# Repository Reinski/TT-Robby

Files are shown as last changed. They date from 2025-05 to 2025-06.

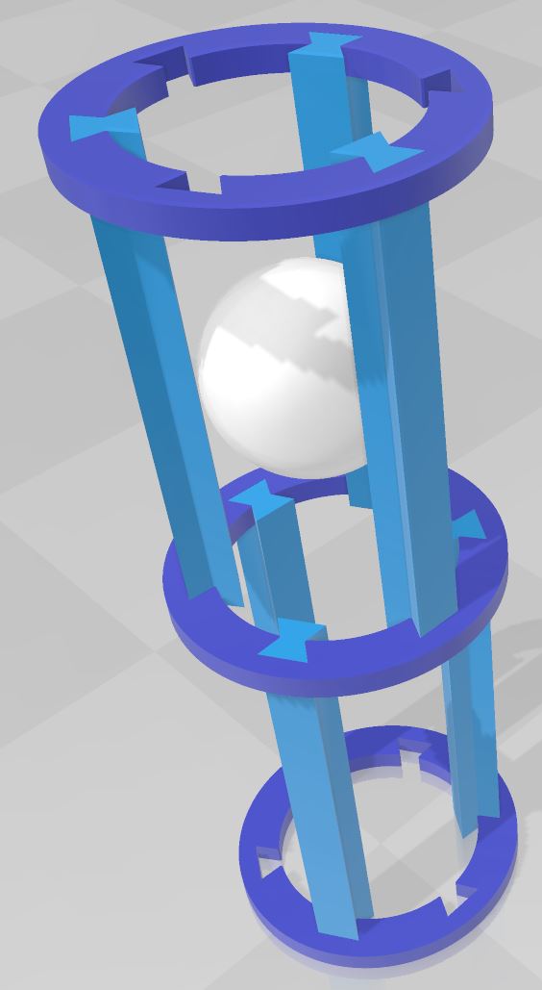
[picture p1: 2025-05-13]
resources/ball_lead_concept.jpg

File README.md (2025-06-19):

# TT-Robby
## Overview
TT-Robby is a hobby project to design a tabletennis ball machine with focus on affordability by hobby players.
The concept is based on using 3D printed parts whereever possible and otherwise cheap components. The tradeoff is a higher requirement of time in comparison to buyable out-of-the-box solutions, invested into printing, assembling and adjusting the whole machine.  
Another goal is high flexibility through modularity in both, construction and programming.
## Getting started
Unfortunately, there is no fool-proof concept that will work out of the box. So this project is still in a tinkering state (PoC). If you want to get a feeling for the basic concept without investing too much time and effort, then I'd suggest the following:
- Print 6x ball_lead-pole_100mm and 3 ball_lead-orthogonal_ring, assemble a straight tube, take a tt-ball and play around with it.
- If you like what you see, print 2 more rings and 3 more poles and add an orthogonal branch in your previous construction (hint: replace one pole with a ring).
- If you still want to continue, then you need to invest some money, as you should start with the electronics now. I find it most satisfying to see the machine fire some balls, so I'd suggest starting with building the Ball Driver:  
  From the BoM below, buy at least 2 DC motors, a raspi pico and the Motor Driver Module plus you'll want some dev equipment like a breadboard, wires, usb-cable etc. plus you'll need some IDE to operate the motors.
- Now, if you're still motivated to go for it, you can have a look at the rest and help finding solutions for all the open issues.
## Bill of material
### Simplest Setup
No side-spin, fix ball direction
- Raspberry Pi Pico W or WH (~8€)
- 2 x DC Toy Hobby Motor - 130 Size 4.5V to 9V (~2€ each)
- 1 x WaveShare DC Motor Driver Module (https://www.waveshare.com/wiki/Pico-Motor-Driver) (~30€)
- 1 x 28BYJ-48 stepper motor 5V DC + ULN2003 driver board (~2.20€ each)
- 2 Rubber rings (50x4mm; Diameter approx. 30mm) 
- Wires + boards
- 3D printing filament
- some tools for printing post-processing and for (dis)assembling (e.g. pliers)
### Max setup
All currently supported features: Top spin, back spin, side-spin, fix ball direction
- Raspberry Pi Pico W or WH (~8€) (Pico2 not tested yet)
- 3 x DC Toy Hobby Motor - 130 Size 4.5V to 9V (~2€ each)
- 1 x WaveShare DC Motor Driver Module (https://www.waveshare.com/wiki/Pico-Motor-Driver) (~30€)
- 2 x 28BYJ-48 stepper motor 5V DC + ULN2003 driver board (~2.20€ each)
- 2 x Sg92r servo motors
- 3 Rubber bands (50x4mm; Diameter approx. 30mm)
- Wires + boards
- 3D printing filament
- some tools for printing post-processing and for (dis)assembling (e.g. pliers)
## Open points
To give a rough overview about the maturity of this project, here are some open issues. Details can be found at the specific components' sections below.
- Ball Feeder with current pushing geometry and stepper motor is not fast enough to serve 1 ball/sec. New conncept is in test, though.
- Concept for Ball Pool must be finalized
- Concept for Ball Recirculation is open
- Concept for Direction Control (automated rotation and tilt) has to be completed. Esp. tilt is missing.
- Power Supply specification for the Ball Driver motors must still be defined.
- Suitability of the 130 size DC toy motors is questionable (although latest tests indicate that two of them are ok for basic funcitonality)
- Wiring and casing geometry is still to be designed
- Control concept and its implementation is incomplete (Controller API)
## Components
This section describes the ball machine's components in detail. The components are listed in alphabetic order.
### Ball Driver
Probably being the most important part of the machine, the Ball Driver is responsible to accelerate the ball with the required attributes of 
- transversal speed
- transversal direction
- spin speed
- spin axis  
  The concept is to have three wheels accelerating the ball from different angles with individual values, so that the forward speed and the rotation speed and axis is determined by the different wheel speeds.
  The forward direction is controlled by the ball lead (always co-axial), so that it can only be controlled by pivoting (left/right) and tilting (up/down) the whole Ball Driver to point into the required direction.
  If a mechanic is implemented to change orientation its minimum requirements shall be:
- pivot angle >= 45°
- tilt angle at least from -45° to +15° (-45° is intended for simulating specific serves, but is certainly not the highest priority)
  In case of downwards tilt a premature release of the ball should be prevented (i.e. gravity should not drag the balls into the driver)
#### Open points
- Power Supply
  Power output from Raspi Pico is too weak for operating the three motors. So a concept is required to provide power to the motors with adequate electrical properties.
  The aim should be:
  - have only one power plug into standard socket (AC)
  - have enough power to operate all motors at full speed
  - have stable power supply for the controller board
  - have the power related elements stored away in some containment to avoid user contact and reduce negative environmental influence (dust, moisture)
  - keep the whole electrical system at an adequate temperature
- Motor Suitability
  The currently used 130 sized DC toy motors are very cheap and have a nice speed, but are very weak and not very responsive to control commands (high inertia-to-power ratio).
  Although they proved capable of driving a ball plain forward at sufficient speed (no spin) - even with just two motors, they must still be testet if they are really suitable under field conditions.
- Orientation Control
  A horizontal swivel has now been designed and seems ok. However, it turns the whole main part of the machine and the decoupling from both, the stand and the Ball Pool, is currently not very satisfying. 
  For the vertical control there is currently no concept implemented.
  A concept should include motor specification, component geometry, ball leading concept for the varying angles.
  Until such a concept is designed, TT-Robby has a fixed ball direction and must be manually oriented into the wanted direction.
- Wiring and Casing
  Wires must be lead in a way that they cannot interfere with the component's operation (turning wheels, moving parts), but still can be easibly mounted and unmounted. This also includes a concept for connectors making the installation more comfortable to the user.  
  Electronic components like the microcontroller on the motor driver shield and also the motors themselves should be located in safe places to provide safety for them and for the operators. An according design is required.
### Ball Feeder
The Ball Feeder has the task to feed the next ball in a controlled manner into the Ball Driver, i.e. directly into the place where the ball is caught by the Ball Driver's wheels. This should happen independently of the Ball Driver's (including the feeder) current orientation, esp. regardless of the relative direction of gravity.
While the Ball Pusher (a turnstile-like design, see below) is able to push a single ball further while holding back the next one, its current geometry prevents it from being able to push the ball far enough into the feeding position.
As an alternative, a piston concept has been designed, which is able to push the ball far enough into the ball driver. However, the current concept takes too long for one sequence, so it needs refactoring.
### Ball Leads
On the whole way from the Ball Pool to the Ball Driver, each ball must always be in a controlled location to avoid disturbances in the operation.
While many machines use tubes or otherwise fully encased constructions to guide the balls in a controlled manner, TT-Robby uses a modular system of combining various segments, basically consiting of 3 co-axial leading poles carried by rings.
The poles are connected to the rings by sticking them through accordingly shaped openings in the rings. Using this principle, more elements can be attached in the same manner either to the rings or to the poles.
### Ball Pool
The Ball Pool is the main reservoir to hold the ball supply for the machine. In normal operation mode it is the only way to feed balls from outside into the machine.  
Designed basically as a big funnel, open at the top and with a ball-sized opening at the bottom, it follows a very simplistic approach.
In the concept phase, a funnel made out of cardboard had been used, which basically fulfilled its task. Meanwhile, a 3d printed ball pool was designed, as integrating the pool in a controlled manner into the machines geometry was problematic with the cardboard-approach.  
However it must be said, that the handling of the 3d-printed ball pool is quite uncomfortable, as it follows the modular concept and as a consequence is not very stable.
#### Open points
- Improve design of the pool itself: It has weak stability when applying force e.g. during assembly.
- Improve ball outlet geometry: Find a statically determined geometry, where all parts go into their pre-defined places.
- Find a concept for reliably supplying balls into the moving part of the machine (i.e. the Ball Driver).
### Ball Pusher
To transport the balls through the whole system (see Ball Leads), finally arriving sequentially at the Ball Driver, they need to be moved independently of their natural tendencies caused by gravity, bouncing etc.  
The Ball Pusher is a cross-shaped wheel (turnstile-like) driven by a step motor, which pushes one ball at a time and lets the next ball move into place. Multiple Ball Pusher components can be attached to Ball Leads whereever required.  
Currently the concept is not used, as instead a more simplistic approach is applied, where the balls are dropping out of the Ball Pool into the Ball Leads and move through them, pulled by gravity.
### Ball Recirculation
After balls have been hit by the player, it would be most convenient to automatically bring them back into the machine, hence creating a full cycle. Most ball machines make use of nets catching the played balls directly near the edges of the table and leading them - dragged by gravity - back into the Ball Pool.  
Despite this being a quite effective concept, it has the downside, that the nets plus their holders are a cost factor and mean quite high effort to assemble before each training session.
Since I am a lazy person, I'm still thinking of an alternative approach.
Until that is found, TT-Robby omits the Ball Recirculation Concept and instead relies on the manual work to collect the served balls and fill them back into the Ball Pool.
### Direction Control / Rotator
The balls' forward direction should be machine-controllable, i.e. the pivot and the tilt of the ball driver must be changeable.  
In the basic setup, this is a manual process by the user simply changing the machine's orientation (see also Machine Mount).
First approach for changing the horizontal direction has been implemented and the name "Rotator" has been established. Since also the tilt is probably controlled by rotation, this name can be used generally.
#### Open Points
- Define overall concept: Orientate the whole machine incl. Ball Pool or orientate just the Ball Driver+Feeder?
- Design mechanical geometry for the selected concept.
- In case of only parts of the whole system change their orientation: Solve problems for a smooth ball transition between static and movable ball leads.
- Define motors to use
- Implement controller logic
### Machine Controller
The Machine Controller is the software running on the Pi Pico and has the task to control the machine parts (motor speeds and orientations). For this it translates the user's requirements (mainly direction, speed, spin and interval) into the technical commands to the motors. It may also be responsible for providing access to the current settings or reflecting them back to the user.
Currently, the plan is to have a REST-API for the user commands which could then be accessed from Apps on a mobile device or even a JavaScript UI running in the local browser.
In its current state the controller program already supports the translation of most user commands into machine control commands and even allows to define ball sequences (changing spin, speed, interval between single balls).
#### Open Points
- REST API
- Security concept (API tokens?)
- Stability tests
- Demonstration UI
### Machine Mount
Where shall TT-Robby be mounted? Currently it must be placed directly on the table surface, but even then it needs some sort of a stand to be designed.  
Idea is to design a simple table surface stand in the first step being easily replacable by other solutions which may be created later.
To achieve this flexibility, a connector concept between the ball machine and the stand shall be implemented.
Options for the stand are:
- Place directly on table
- Attach to table by clamp or something similar
- Place on an own stand (maybe attach to standard camera tripod)
- Direction Control could be implemented in the stand and not into the ball machine itself
#### Open Points
- Design mount connectors
- Design simple stand
- Design flexible mount, allowing rotation and tilt - if this is not a feature of the ball driver alone.
## Specifications
These are the minimum specifications that should be met by the fully configured machine.
- As cheap as possible
- Shot frequency: 1 balls/sec
- Ball forward speed: 100 km/h
- Ball rotation: up to 100 rpm
- Shot direction angle, horizontal rotation: 90°
- Shot direction angle, up/down: 45°
- Fully Controllable via App

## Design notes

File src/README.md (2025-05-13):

# Robby Machine Controller
## General Overview
The Machine Controller is the micropython software that controls the operation of the ball machine. It provides an http REST-API to be called by any clients.  
Currently, the machine controller is designed to run a single Raspberry Pi Pico W and even only on a single core, due to problems with multiprocessing under micropython.
## Installation
The machine controller must be transferred onto the Pico board by flashing the micropython firmware.  
... description to be done ...
## Calibration
Due to the lack of sensors which could report the actual positions of movable parts, the software must keep track about this itself. Therefore it must have a known starting point (defined position of all movable parts) into which all parts must be brought manually before using the machine. This is the purpose of the machine calibration routine.  
... description to be done ...
## Controller Description
### Mode of Operation
The most basic setting of the machine is its mode of operation:
- calibration mode
  Before the machine can start operating, all movable parts must be brought to a defined position.
- continuous mode
  When started, the machine is playing the same shots in a constant interval until it is stopped.
- program mode
  When started, the machine is playing shots following the selected program until it is stopped. A program defines a sequence of shots that can differ in speed, spin and timing. 
### Calibration
### Continuous Mode
This is the most basic mode, as it keeps playing the same balls over and over again, until it is stopped.  
Parameters are:
- ball speed
- ball spin
- pause time before next shot
### Program Mode
The machine can execute predefined shot cycles, so-called programs. A program consist of multiple shots, where each shot has these parameters:
- ball speed
- ball spin
- pause time before next shot
- number of repetitions (default: 1)
- pause time between repetitions (default: pause time before next shot)
Planned extensions:  
When the machine supports automatic tilt and swivel, then these parameters can be added:
- swivel angle
- tilt angle

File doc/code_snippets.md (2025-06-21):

# Code snippets
## REPL
These snippets can be executed directly in the REPL.
### Create controller object
Import the library and create an instance of RobbyController.
```python
from lib.RobbyController import RobbyController
controller = RobbyController(debug=True, no_server=True)
print(f"Current state: {controller.mode_text} ({controller.mode}), {controller.status_text} ({controller.status})")
```
This does three things:
1) enable debug messages
2) prevent the REST-API webserver from being started
3) print the current state of the machine
Unfortunately, the controller becomes unresponsive or gets other problems if the webserver is started.
### Configuration mode
The following lines enable the configuration mode and prints the current config and status of the machine. Finally it prints the full config of the first ballbriver.
```python
controller.mode = 2
print(f"Current state: {controller.mode_text} ({controller.mode}), {controller.status_text} ({controller.status})")
print(controller.getConfigData())
print(controller.getStatusData())
print(controller.ball_drivers[0].getConfigData())
```
Note that the getConfigData methods are returning dictionaries, which is useful when building APIs for external clients and which is actually used for the existing REST-API. The same dictionary structure can be used to modify the configuration as a whole (Now we use a ball_feeder, as this is not yet implemented for ball_drivers):
```python
config = controller.ball_feeders[0].getConfigData() # receive the current config
config['bf_index'] = 1                              # change something in the config
controller.ball_feeders[0].setConfigData(config)    # pass the whole changed config back
print(controller.ball_feeders[0].getConfigData())   # see that the changes were adopted
```
Note that this example doesn't necessarily make any sense. ;-)  
#### Test ball driver
You can use the config mode for testing your setup. E.g. test the ball driver motors by executing this line by line and see what happens:
```python
controller.mode = 2                                             # activate config mode
controller.ball_drivers[0].update_current_shot(v_ball_norm=.75) # change the ball speed for current shot to 75%
controller.ball_drivers[0].start()                              # start the ball driver with this setting
controller.ball_drivers[0].update_current_shot(v_ball_norm=.5)  # reduce the ball speed to 50%
controller.ball_drivers[0].stop()                               # stop all ball driver motors
```
You can also test the individual motors:
```python
controller.ball_drivers[0].motors[1].start()       # start the 2nd motor of first ball driver
controller.ball_drivers[0].motors[1].set_speed(75) # set its speed to 75%
controller.ball_drivers[0].motors[1].stop()        # stop the motor again
```
#### Test ball feeder
```python
controller.mode = 2                                  # activate config mode
controller.ball_feeders[0].dispense()                # execute the cycle for dispensing one ball
print(controller.ball_feeders[0].getConfigData())    # get the ball feeder's configuration
print(controller.ball_feeders[0].motor_states[0][1]) # print the action cycle (last index 1) of the frist motor (index 0) of the first feeder (index 0)
controller.ball_feeders[0].stop()                    # stop all ball feeder motors (in case they are still running)
```

### Direct Control mode
```python
controller.mode = 0
print(f"Current state: {controller.mode_text} ({controller.mode}), {controller.status_text} ({controller.status})")
``` 
This enables the direct mode, which repeats the same shot in a fixed interval. However, it allows direct adjustment of the shot's properties, even during playing.
```python
cs_cfg = controller.ContinuousShot.getConfigData() # get the current shot config
print(cs_cfg)                                      # display it
# now let's increase the time between shots by 1 second
controller.update_continuous_shot(bd_number=cs_cfg['bd_number'], pause_seconds=cs_cfg['pause']+1.0)
print(cs_cfg)                                      # display the updated shot
```
Basically, the code should look something like this - but unfortunately the controller becomes unresponsive after some seconds (a bug probably related to the StepMotors and PIO):
```python
controller._start_playing()                              # start playing with the current shot settings
controller.update_continuous_shot(0, 1.0, 0.0, 0.0, 2.0) # modify the current shot settings
controller._stop_playing()                               # stop playing
```
### Program mode
```python
controller.mode = 1
print(f"Current state: {controller.mode_text} ({controller.mode}), {controller.status_text} ({controller.status})")
```
This enables the program mode, which plays predefined sequences of shots.

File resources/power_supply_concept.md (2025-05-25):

```[5V Netzteil / Step-Down]
        |
        +--> VIN Waveshare Board --> DC-Motoren (TB6612)
        +--> ULN2003 VCC ---------> Stepper (28BYJ-48)
        +--> Servo VCC ------------> SG92R
        |
       GND ------------------------+
                                   |
                        +----------+----------+
                        |                     |
                [Raspberry Pi Pico W]     [Alle Module]
                   (USB / VSYS)             (GND gemeinsam)```

### 🗲 Kostengünstiges Stromversorgungskonzept

*(1 × 230 V‑Stecker, versorgt alle Motoren + Pico‑W sicher)*

| Variante                   | Bauteil                                                                    | Daten & Preis (D‑/EU‑Straßenpreis) | Pro / Contra                                                                                           | Empfehlung                           |
| -------------------------- | -------------------------------------------------------------------------- | ---------------------------------- | ------------------------------------------------------------------------------------------------------ | ------------------------------------ |
| **A** (Ein­netzteil)       | **5 V / 10 A Schaltnetzteil**<br>‑ Mean Well RS‑50‑5<br>‑ Joy‑IT EPS‑65‑05 | 50 W, Schraubklemmen<br>10–15 €    | + nur 1 Gerät<br>+ intern geregelt/geschützt<br>+ Erdung möglich<br>− offenes Netzteil – Gehäuse nötig | **Beste Preis‑Leistung**             |
| **B** (Hutschiene)         | **DIN 5 V / 8 A** (z. B. HDR‑60‑5)                                         | 60 W, Hutschiene<br>17–20 €        | + saubere Montage<br>− Hutschine/Box nötig                                                             | ok, falls Schaltschrank vorhanden    |
| **C** (“Handy‑Ladegeräte”) | 2 × USB‑PD‑Netzteile (5 V / 3 A) + 1 × USB 5 V / 2 A                       | 3 × 6 € ≈ 18 €                     | + überall verfügbar<br>+ gleich Kabel<br>− 3× Steckdose<br>− keine Masse‑Klemme                        | nur wenn Gehäusefrei + steckdosen ok |
| **D** (PC‑Netzteil)        | Micro‑ATX PSU gebraucht                                                    | 5 V 15–20 A                        | + Spottbillig (5 – 10 €)<br>+ Lüfter schon drin<br>− groß, laut<br>− ATX‑Power‑On‑Hack nötig           | nur bei Platz & Lautstärke egal      |

---

## Dimensionierung

| Last             | Strom (Spitze)               | Reserve‑Faktor | Budgetiert  |
| ---------------- | ---------------------------- | -------------- | ----------- |
| 3 × 130‑DC‑Motor | 0,8 A ea. (\*Anlauf ≈ 1,5 A) | ×1,5           | 4 A         |
| 2 × 28BYJ + ULN  | 0,24 A ea.                   | ×1,2           | 0,6 A       |
| 3 × Servo SG90   | 0,7 A ea. (Stall)            | ×1,2           | 2,5 A       |
| Pico W + Boards  | 0,2 A                        | ×1             | 0,2 A       |
| **Summe**        |                              |                | **≈ 7,3 A** |

→ **5 V / 8 A min.**, besser 10 A.

---

## Empfohlene Umsetzung (Variante A)

1. **Mean Well RS‑50‑5**

   * 230 V → 5 V 10 A, \~12 €.
   * Schraubklemmen: L, N, PE / +5 V, GND.
2. **Verkabelung**

   * **+5 V** zu VIN des Waveshare‑Boards (speist DC‑Motoren).
   * **+5 V** weiterverteilt an ULN2003 + Servos (über 2,5 mm² Verteilklemme).
   * **Pico W**:

     * Entweder USB‑Netzteil (sauberste Trennung).
     * **Oder** zweite Leitung +1 000 µF Elko → VSYS, wenn nur ein Netzteil gewünscht.
3. **Entstörung**

   * Jeder Servo + Stepper: 100 nF KerKo zwischen VCC/GND.
   * DC‑Motoren: 100 nF Motoranschlüsse + 220 µF Elko am TB6612‐VIN.
4. **Gehäuse / Sicherheit**

   * RS‑50‑5 in gedrucktem oder Metall‑Kleingehäuse; PE (Schutzleiter) anschließen.
   * Primärseite abgedeckt, Lüftungsschlitze nach oben.
5. **Kosten**

   * Netzteil 12 €
   * Verteilklemmen, Elkos, Kabel ≈ 6 €
   * Gesamt **< 20 €** für komplette 230 V → 5 V 10 A‑Versorgung.

---

### Warum nicht mehrere Handy‑Netzteile?

* Kein gemeinsamer Massenknoten → mehr Gleichtakt­störungen.
* Mehr Steckdosen, mehr Kabelsalat.
* Trotz ähnlichem Preis weniger stabil bei Anlauf­strömen (OTP/OPP).

---

## Schnell‑Checkliste zum Aufbau

* [ ] Netzteil 5 V ≥ 10 A installiert & geerdet
* [ ] 2,5 mm² Haupt‑Versorgungs­kabel zu Motor‑/Servo‑Verteilung
* [ ] 470‑µF Elko nah am Waveshare‑VIN
* [ ] Separate 5 V‑Leitung (oder USB) für Pico W
* [ ] Sterne‑Ground: alle GND an einem Schraubklemmen­block
* [ ] Leitungs­querschnitte: Motor ≥ AWG 20, Servo AWG 24, Signal AWG 26–28
* [ ] Sicherung (z. B. 2 A träge) in Primär­leitung oder Polyfuse 8 A sekundär

Damit hast du eine **kostengünstige, nur 1× 230 V‑Stecker**‑Lösung, die alle Motoren und den Pico zuverlässig versorgt.

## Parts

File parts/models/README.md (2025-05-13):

# parts/models/
This folder and its subfolders contain the 3d models used in the project. There may be untested or even obsolete models.  
The parent folder itself contains models that are generally not yet sorted into one of the subfolders. Files from the parent folder will be moved into the appropriate subfolders in the future.  
## Subfolders
- ```./prod/```  
  Contains models that are tested and recommended for use in the machine.
- ```./in_development/```  
  Contains models that are untested or currently in design or test-phase. Use on your own risk.
- ```./templates/```  
  Contains models that are not directly used for the machine, but rather support design process. These can be negatives to substract from other geometries, i.e. they are a slightly oversized, so that the according positives can fit in. Others can be positives which can be re-used when designing new machine parts.

## Conventions
### File Format
As an application and platform independent format, ```.obj``` is preferred. Alternatively ```.stl``` can be used.  
As additional format ```.3mf``` is permitted, as this is also an open format and provides additional benefits - at least for my setup using Windows and a BambuLab printer: Windows Explorer can show a preview for .3mf files and Bambu Studio also uses this format.
### File Names
Naming should basically describe the model. Multiple name-parts are separated by hyphen (-). Multiple words within one name-part should be separated by underscore (_), aka snake-case.  
The following name-parts are obligatory:
- "TT-Robby" (maybe just "TTRobby" in future) has been established as a prefix.
- machine component name
- part specifyer

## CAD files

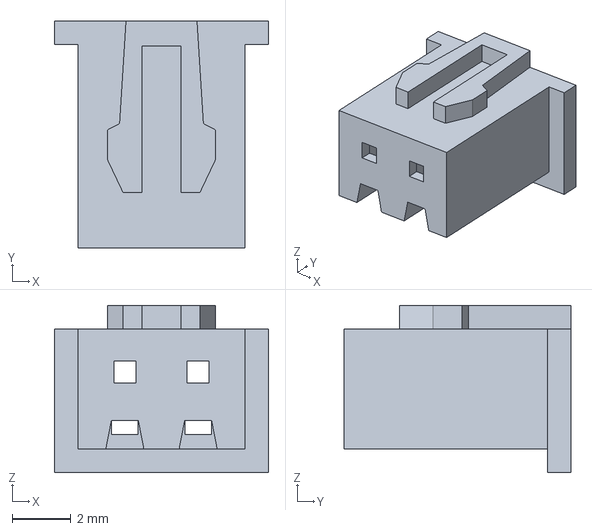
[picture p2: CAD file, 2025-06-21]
parts/models/in_development/JST-XHP-1S-genuine.3mf
7.30 x 7.75 x 5.70 mm

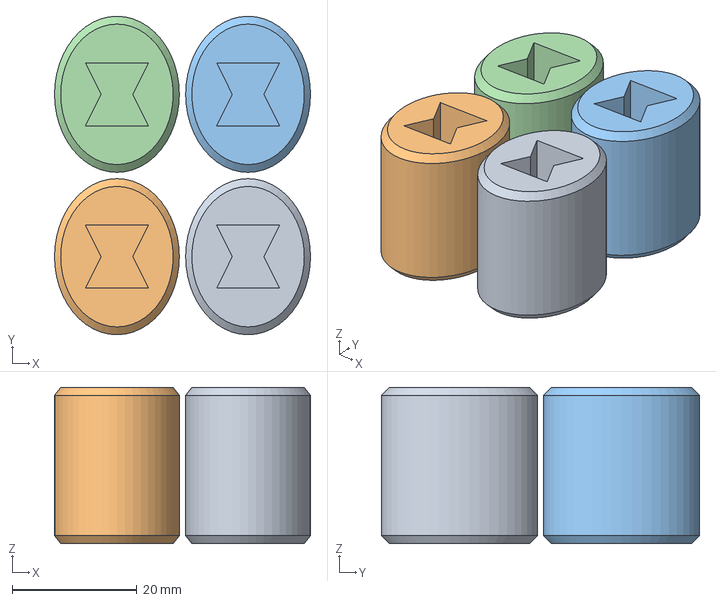
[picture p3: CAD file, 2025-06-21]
parts/models/prod/TT-Robby-stand-pole_connector.3mf
41.0 x 51.0 x 25.0 mm
TT-Robby-stand-pole_connector.obj x 4

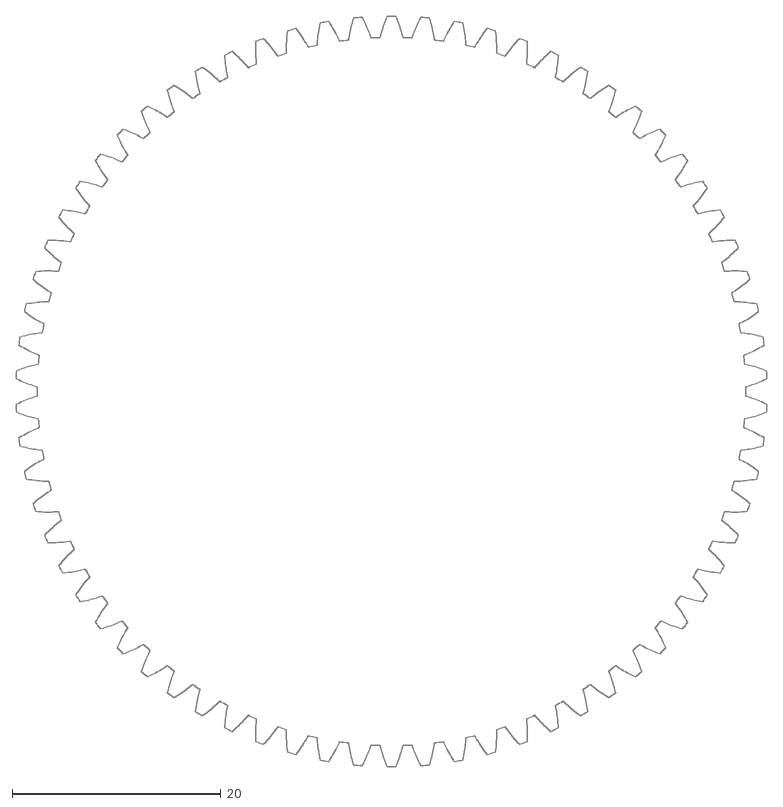
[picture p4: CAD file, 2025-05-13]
parts/models/templates/involute_gear_70mm_70.dxf
72.0 x 72.0

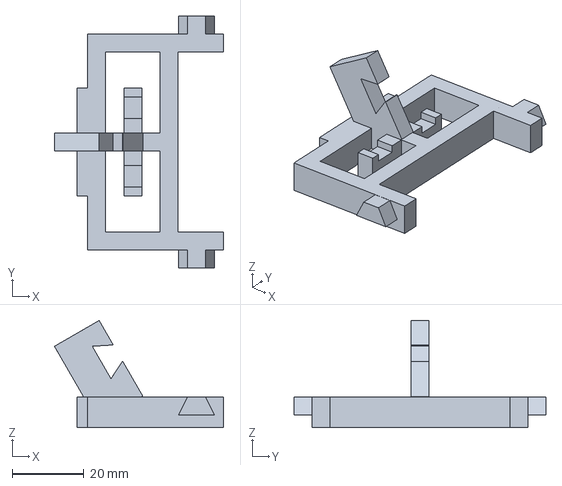
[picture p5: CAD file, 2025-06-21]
parts/models/TT-Robby-ball_driver-v4bottom.3mf
47.0 x 70.0 x 29.7 mm

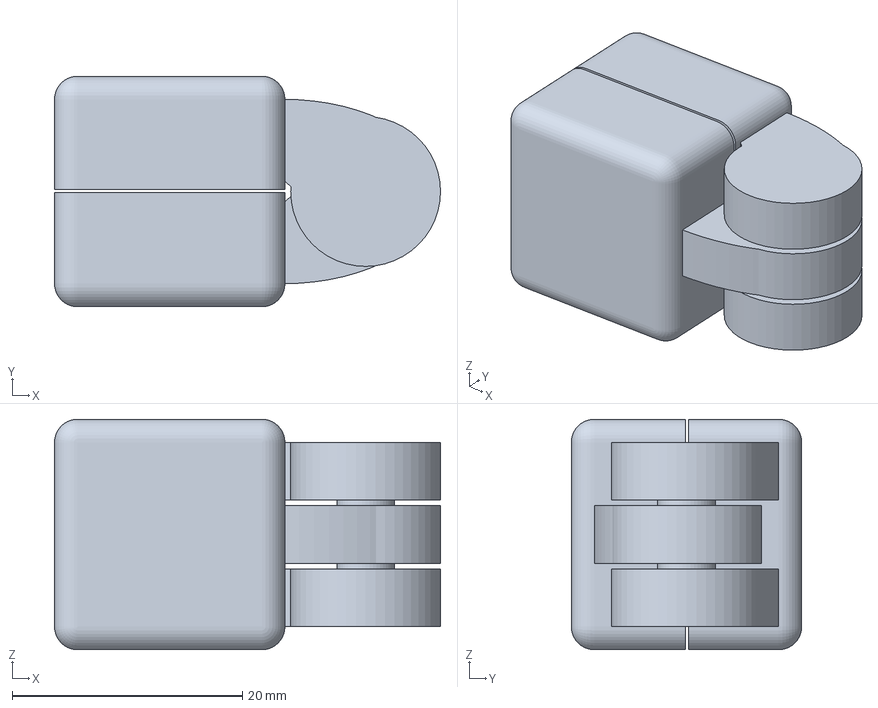
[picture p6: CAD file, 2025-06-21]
parts/models/in_development/TTRobby-ball_lead-ring_joint.3mf
33.5 x 20.0 x 20.0 mm

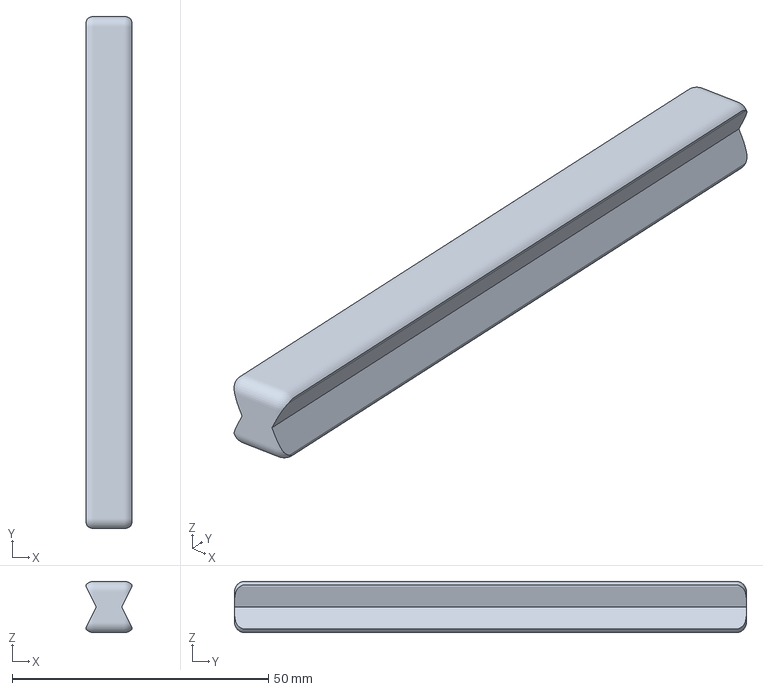
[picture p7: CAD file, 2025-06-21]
parts/models/prod/TTRobby-tools-pole_rounded.3mf
8.99 x 100.0 x 10.0 mm

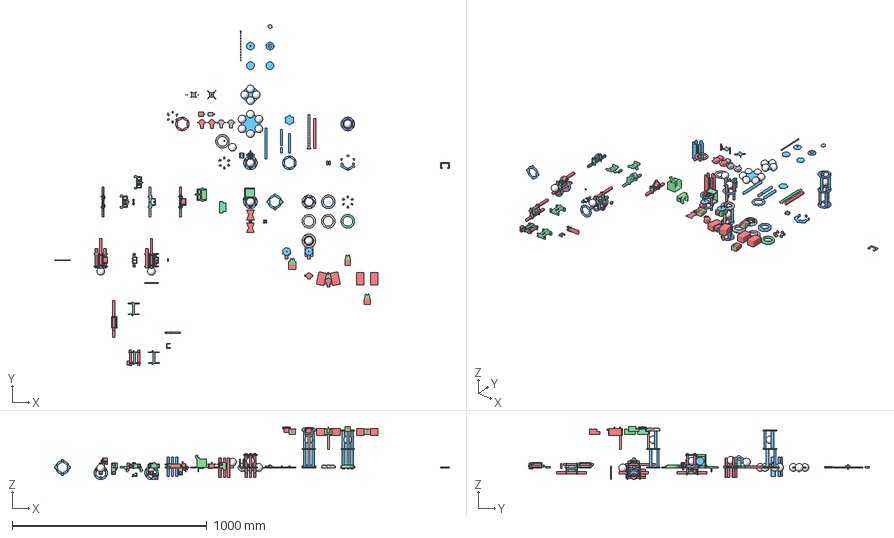
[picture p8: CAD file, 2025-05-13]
parts/models/templates/TT-Robby-templates.3mf
2029.4 x 1751.5 x 273.8 mm

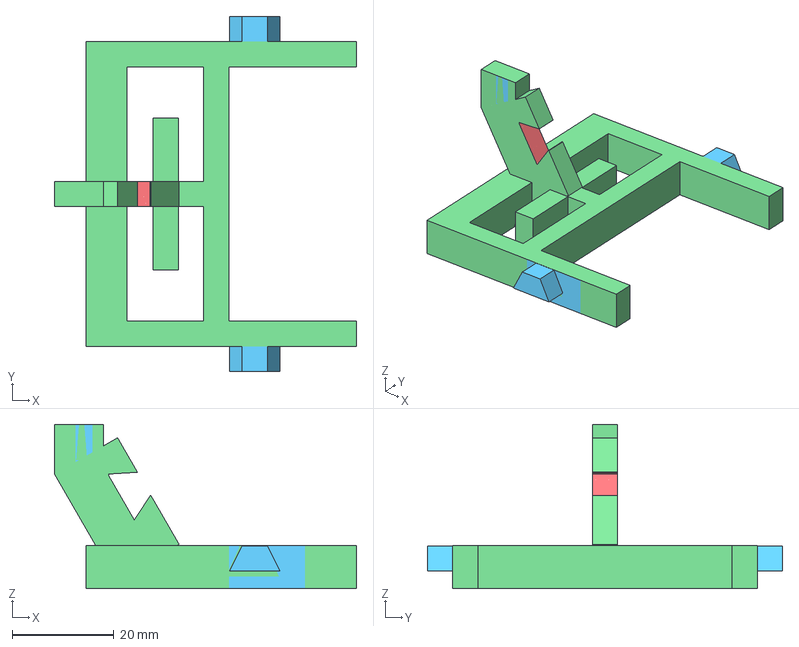
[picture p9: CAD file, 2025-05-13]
parts/models/TT-Robby-ball_driver-v3bottom.3mf
59.5 x 70.0 x 32.4 mm

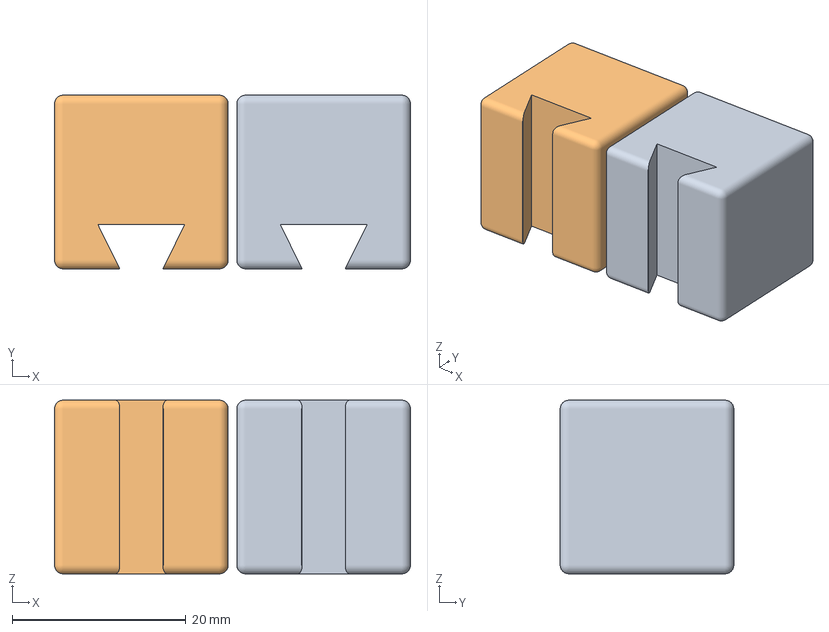
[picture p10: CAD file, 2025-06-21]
parts/models/prod/TTRobby-pole-connector_90deg.3mf
41.0 x 20.0 x 20.0 mm
TTRobby-pole-connector_90deg.obj x 2

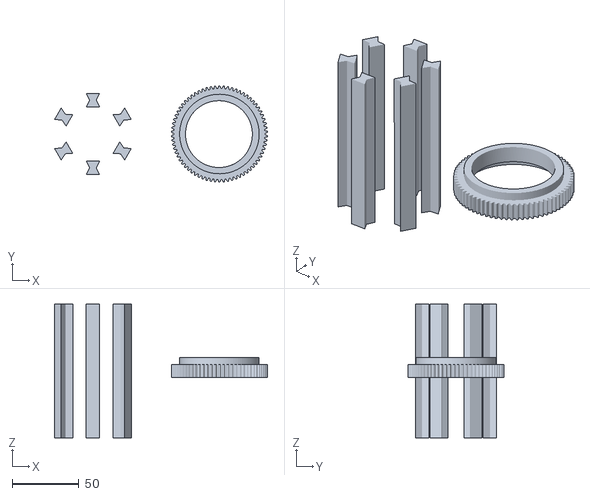
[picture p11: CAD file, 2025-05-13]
parts/models/templates/TT-Robby-ball_lead-termination-cogwheel-template.obj
159.3 x 72.0 x 100.0

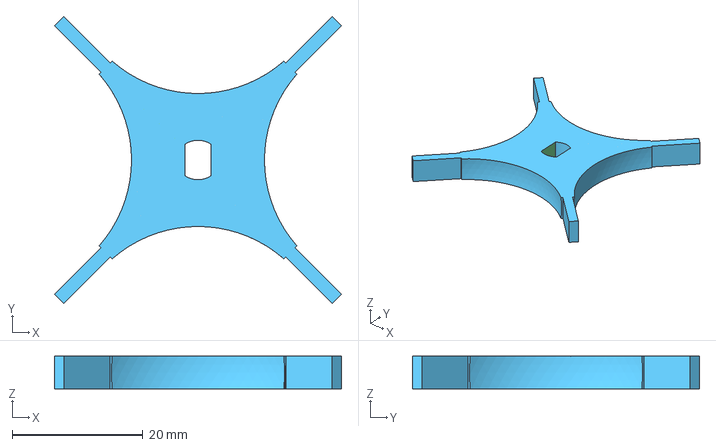
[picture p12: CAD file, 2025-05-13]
parts/models/TT-Robby-ball_rocker.3mf
43.8 x 43.8 x 5.00 mm

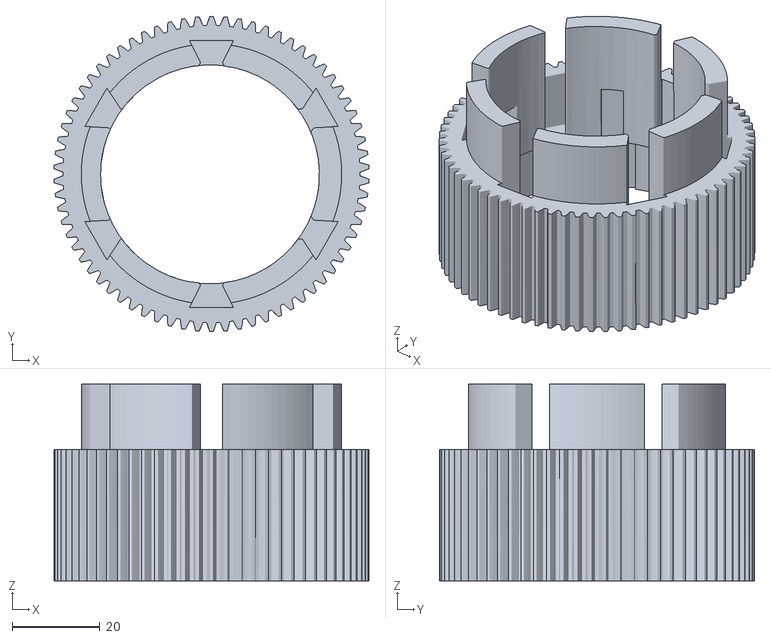
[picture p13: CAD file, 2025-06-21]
parts/models/in_development/TTRobby-ball_lead-termination-cogwheel-ring-3timesLength_experiment.obj
72.0 x 72.0 x 45.0

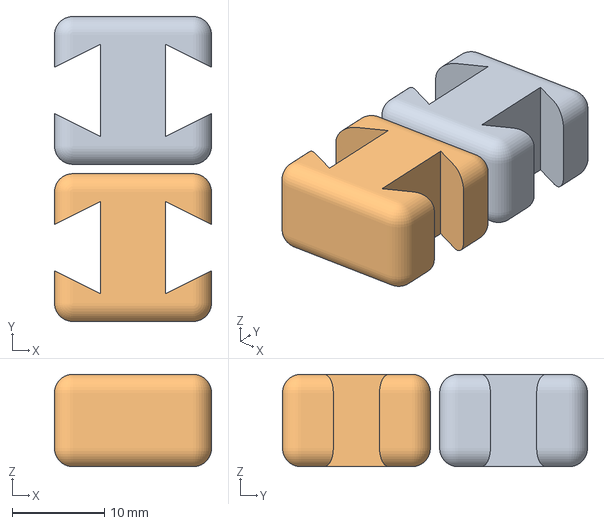
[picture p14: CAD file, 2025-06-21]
parts/models/prod/TTRobby-pole-spacer_parallel.3mf
17.0 x 33.0 x 10.0 mm
TTRobby-pole-spacer_parallel.obj x 2

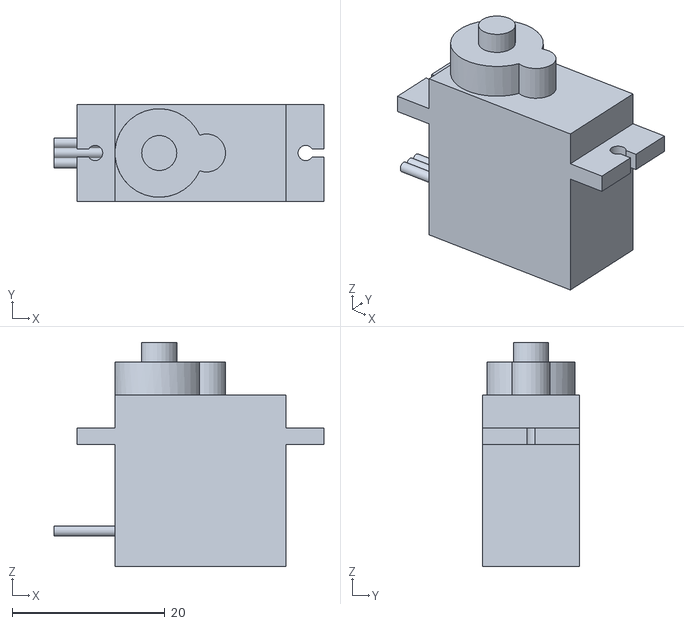
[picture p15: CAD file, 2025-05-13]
parts/models/templates/SG92R.obj
35.4 x 12.7 x 29.4

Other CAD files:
parts/models/TT-Robby-rotator-motor_holder.stl
parts/models/prod/TT-Robby-ball_lead-pole_100mm.3mf
parts/models/templates/TT-Robby-tube_templates.3mf
parts/models/TT-Robby-ball_driver-bottom.3mf
parts/models/TT-Robby-ball_driver-bottom.stl
parts/models/TT-Robby-ball_driver-frame.3mf
parts/models/TT-Robby-ball_driver-frame.stl
parts/models/TT-Robby-ball_driver-v2bottom.3mf
parts/models/TT-Robby-ball_driver-v2bottom.stl
parts/models/TT-Robby-ball_driver-v3bottom.stl
parts/models/TT-Robby-ball_driver-v4bottom.stl
parts/models/TT-Robby-ball_driver-wheel_20mm.3mf
parts/models/TT-Robby-ball_driver-wheel_20mm.stl
parts/models/TT-Robby-ball_lead-3-spares.3mf
parts/models/TT-Robby-ball_lead-3-spares.stl
parts/models/TT-Robby-ball_lead-6-spares.3mf
parts/models/TT-Robby-ball_lead-6x10.2_spares.3mf
parts/models/TT-Robby-ball_lead-orthogonal_ring_3conn.3mf
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

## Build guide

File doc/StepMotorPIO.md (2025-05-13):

# Controlling Stepper Motor via Raspberry Pi Pico PIO and MicroPython
## Concept
PIO state machines are used to asynchronously operate the stepper motor, so that the main program is not blocked.
### Main Program Controller
This is a micropython program for these top-level tasks:
- Holds constant data definitions, like pin numbers, step sequences etc.
- Controls dynamic operation parameters, like number of steps, motor speed
- Starts and stops motor operation
- Converts data into appropriate units/formats where required
### PIO – SM1
This is the top-level state machine and its tasks are:
- Trigger each motor step
- Keep track of the number of steps left to go
- Inform the main program when it is finished

Input parameters (pulled from TX-queue):
- Number of steps
### PIO – SM2
This state machine is mainly for controlling the speed and has these tasks:
- Wait for trigger from SM1
- Trigger single motor step
- Take care about the time delay to next motor step

In case speed is constant, this SM can be omitted and SM1 can trigger SM3 directly
### PIO – SM3
This state machine has these tasks:
- Wait for trigger from SM2 (or from SM1 if speed is constant)
- Take care about the pin settings for the next step
- Control the output pins

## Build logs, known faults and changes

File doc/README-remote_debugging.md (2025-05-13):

<!--
 Copyright (c) 2023 Reiner Nikulski
 
 This software is released under the MIT License.
 https://opensource.org/licenses/MIT
-->
# DebugProbe
Unfortunately, via the pico-w-go extension it is not possible to interactively debug code (i.e. set breakpoints, step through etc.) running on a directly connected pico.
One solution is using another Raspberry Pi Pico as a debug probe, which means it works as a USB to SWD/UART bridge.
The debug probe is then connected to your PC and the target pico is connected to the probe.
This approach to achieve interactive debugging functionality in VSCode is described here.
It is based on the official getting-started documentation: https://datasheets.raspberrypi.com/pico/getting-started-with-pico.pdf.
More unfortunately: All effort failed! There doesn't seem to be a way to interactively debug micropython programs running on a pico 

## Software requirements
- VSCode
- openOCD
- debugprobe.uf2 or picoprobe.uf2
## Hardware requirements
- Windows PC as development platform (tested on Windows 10 Pro)
- Raspberry Pi Pico as debug probe (tested with basic pico w/o WLAN)
- Raspberry Pi Pico as the target pico, which needs to be debugged
- Breadboard(s) for wiring it all together
## Skill requirements
- Browsing the internet & Downloading software
- Sticking pins or wires into the right holes on a breadboard
- Soldering (can possibly get around it if the Picos do already have headers --> H-variants)
- For this documentation: Some basic skill to handle files and folders in Windows and at the command prompt (cmd.exe)

## Installation
### Install VS Code and extensions
The installation of VSCode is not covered here. Extensions I used in the given context:
- Python by MS
- Pylance by MS
- Pico-W-Code by paulober
All extensions could be installed as described in their documentation.
### Flash debug probe
- From [github repository](https://github.com/raspberrypi/picoprobe/releases) download
  - debugprobe.uf2 (or picoprobe.uf2)
- Connect the debug probe via USB cable to your running Windows PC:
  - Hold down the BOOTSEL button
  - Connect probe via USB to PC
  - Wait until explorer opens the pico as new usb drive
    If that doesn't happen, you might have a poor usb cable (no data wires), so try another one.
  - Release the BOOTSEL button
  - Copy the .uf2 file to the usb drive (root folder)
    The drive will immediately dissappear, as the pico starts flashing its firmware.
    In my case, Windows informed me after some seconds, that a new device was ready for use, which I took as confirmation that flashing was successful.
    Also, the LED on the pico will be turned on.
  
### Flash target pico
- Download the uf2 file for micropython from (...)
- Hold down the BOOTSEL button
- Connect probe via USB to PC
- Wait until explorer opens the pico as new usb drive
  If that doesn't happen, you might have a poor usb cable (no data wires), so try another one.
- Release the BOOTSEL button
- Copy the .uf2 file to the usb drive (root folder)
  The drive will immediately dissappear, as the pico starts flashing its firmware.
  In my case, Windows informed me after some seconds, that a new device was ready for use, which I took as confirmation that flashing was successful.

### Install openOCD
- Search and download precompiled binaries/package for Windows
- Simply copy the main folder into the programs folder of your Windows
- Test installation:
  - Open cmd.exe
  - Go into the installation folder "OpenOCD-..."
  - run openOCD:  
    ```bin\openocd.exe```  
    If you see something like this, then it was a success:
    ```Open On-Chip Debugger 0.12.0 (2023-06-21) [https://github.com/sysprogs/openocd]
    Licensed under GNU GPL v2
    libusb1 09e75e98b4d9ea7909e8837b7a3f00dda4589dc3
    For bug reports, read
            http://openocd.org/doc/doxygen/bugs.html
    embedded:startup.tcl:28: Error: Can't find openocd.cfg
    in procedure 'script'
    at file "embedded:startup.tcl", line 28
    Info : Listening on port 6666 for tcl connections
    Info : Listening on port 4444 for telnet connections
    Error: Debug Adapter has to be specified, see "adapter driver" command
    embedded:startup.tcl:28: Error:
    in procedure 'script'
    at file "embedded:startup.tcl", line 28
    ```
### Wire your devices
Connect debug probe with target pico and finally plug the usb cable from the debug probe into the PC.
Wiring can be found in the official getting-started documentation in Appendix A (link see on top), 
### Check connection
According to the docs, this line should somehow signal you success (I guess, the referenced cfg files need not exist(?)):  
```bin\openocd -f interface/cmsis-dap.cfg -c "adapter speed 5000" -f target/rp2040.cfg -s tcl```  
However, I only receive this:
```Open On-Chip Debugger 0.12.0 (2023-06-21) [https://github.com/sysprogs/openocd]
Licensed under GNU GPL v2
libusb1 09e75e98b4d9ea7909e8837b7a3f00dda4589dc3
For bug reports, read
        http://openocd.org/doc/doxygen/bugs.html
adapter speed: 5000 kHz
Info : Hardware thread awareness created
Info : Hardware thread awareness created
Info : Listening on port 6666 for tcl connections
Info : Listening on port 4444 for telnet connections
Info : Using CMSIS-DAPv2 interface with VID:PID=0x2e8a:0x000c, serial=E6616408437D1831
Info : CMSIS-DAP: SWD supported
Info : CMSIS-DAP: Atomic commands supported
Info : CMSIS-DAP: Test domain timer supported
Info : CMSIS-DAP: FW Version = 2.0.0
Info : CMSIS-DAP: Interface Initialised (SWD)
Info : SWCLK/TCK = 0 SWDIO/TMS = 0 TDI = 0 TDO = 0 nTRST = 0 nRESET = 0
Info : CMSIS-DAP: Interface ready
Info : clock speed 5000 kHz
Error: Failed to connect multidrop rp2040.dap0
```
According to internet sources, this means, debug probe was found, but the connection to the taget pico is not working.
Options:
- Check all cables - OK
- Try other target pico - non available
- Try with picoprobe.uf2 instead debugprobe.uf2
- openocd language dependent? -> micropython
- usb driver??

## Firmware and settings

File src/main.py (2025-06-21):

# TT-Robby
# Copyright (c) 2025 Reiner Nikulski
# 
# This software is released under the MIT License.
# https://opensource.org/licenses/MIT
from lib.RobbyController import RobbyController
from lib.WebServer import WebServer
from machine import Pin

if __name__ == "__main__":
    print(f"Signal 'execution started' by switching LED on.")
    pin = Pin("LED", Pin.OUT)
    pin.on()
    print("Initializing.")
    # start web server
    try:
        webserver = WebServer(debug=True)
        try:
            controller = RobbyController(no_server=True, debug=True)
        except Exception as e:
            print(f"Cannot initialize RobbyController: {e}")
        webserver.run(controller)
    except KeyboardInterrupt:
        pass
    except Exception as e:
        raise e
    finally:
        pin.off()

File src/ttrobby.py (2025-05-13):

# TT-Robby
# Copyright (c) 2023 Reiner Nikulski
# 
# This software is released under the MIT License.
# https://opensource.org/licenses/MIT
from lib.RobbyController import RobbyController
from lib.WebServer import WebServer
from utime import sleep

def perform_test():
    # perform a test run for 60s
    print(f"Execution started")
    controller = RobbyController()
    try:
        print(f"RobbyController initialized")
        controller._start_playing()
        print(f"Started playing")
        sleep(60)
        print(f"Slept for 30 sec")
        controller._stop_playing()
        print(f"Stopped playing")
    except KeyboardInterrupt:
        print(f"Interrupted")
        controller._stop_playing()
        print(f"Stopped playing after interrupt")
    except Exception as e:
        print(f"Exception caught: {e}")
        controller._stop_playing()
        print(f"Stopped playing after exception")
        raise e    

if __name__ == "__main__":
    webserver = WebServer(debug=True)
    controller = RobbyController(no_server=True, debug=True)
    webserver.run(controller)

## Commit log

2025-05-25 reorganize models
    [TT-Robby-ball_driver-wheel-flat_20mm.3mf, TT-Robby-ball_driver-wheel-flat_20mm.stl, TT-Robby-ball_lead-orthogonal_ring.3mf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]
2025-05-29 extend motor calibration functions
2025-06-21 update models, new feeder (archimedes screw)
    [JST-XHP-1S-genuine.3mf, TT-Robby-ball_driver-v4bottom.3mf, TT-Robby-ball_lead-pole_100mm.3mf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]
